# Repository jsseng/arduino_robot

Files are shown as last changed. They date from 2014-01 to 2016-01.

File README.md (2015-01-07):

arduino_robot
=============

A controllable arduino robot aimed towards elementary students to get them introduced
to computing at an early age. Comes with firmware and software including a
custom programming language tailored for simple use by students. The grammar
is defined [here](PurelyGrammar.pdf).

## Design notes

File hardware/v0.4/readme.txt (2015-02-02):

Note:  Excellon drill file resolution at 5 digits

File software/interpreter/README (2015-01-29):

To run the java program...

java Interpreter -dumpAST <STUDENT_SOURCE_FILE>

There is a script to interpret a file then avr-gcc it onto the board
It will overwrite arduino_robot/firmware/testing/main.c

./avrcompile <STUDENT_SOURCE_FILE>

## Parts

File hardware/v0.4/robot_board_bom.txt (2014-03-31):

"Qty";"Value";"Device";"Package";"Parts";"Description";"PROD_ID";"VALUE";
"1";"";"M03PTH";"1X03";"IR";"Header 3";"";"";
"3";"";"M03X22X3_SILK_SM";"2X3";"JP8, JP10, JP11";"2x3 .1" header.";"";"";
"3";"";"M04PTH";"1X04";"JP3, JP6, JP7";"Header 4";"";"";
"1";"";"M06SIP";"1X06";"JP5";"Header 6";"";"";
"2";"";"M081X08";"1X08";"JP1, JP4";"Header 8";"";"";
"2";"";"TAC_SWITCHPTH";"TACTILE-PTH";"RESET, S2";"Momentary Switch";"";"";
"5";".1uF";"C-USC1206";"C1206";"C4, C5, C6, C8, C10";"CAPACITOR, American symbol";"";"";
"1";"1.5K";"R-US_R1206";"R1206";"R53";"RESISTOR, American symbol";"";"";
"1";"100K";"R-US_R1206";"R1206";"R44";"RESISTOR, American symbol";"";"";
"2";"100K 1%";"R-US_R1206";"R1206";"R45, R46";"RESISTOR, American symbol";"";"";
"1";"100uF";"CAP_POLD";"PANASONIC_D";"C3";"Capacitor Polarized";"";"";
"8";"10K 1%";"R-US_R1206";"R1206";"R27, R37, R38, R40, R42, R54, R58, R60";"RESISTOR, American symbol";"";"";
"2";"1206PPTC_FUSE";"1206PPTC_FUSE";"R1206";"F2, F3";"";"";"";
"1";"120K 1%";"R-US_R1206";"R1206";"R35";"RESISTOR, American symbol";"";"";
"1";"16MHz";"CRYSTAL10.5X4.8";"CRYSTAL-SMD-10.5X4.8-2PIN";"Y1";"Various standard crystals. Proven footprints. Spark Fun Electronics SKU : COM-00534";"";"";
"8";"1K";"R-US_R1206";"R1206";"R39, R43, R55, R56, R59, R61, R63, R65";"RESISTOR, American symbol";"";"";
"1";"1M";"R-US_R1206";"R1206";"R28";"RESISTOR, American symbol";"";"";
"1";"1uF";"C-USC1206";"C1206";"C9";"CAPACITOR, American symbol";"";"";
"1";"1uH";"TAIYO4012";"TAIYO4012";"U$4";"";"";"";
"5";"20K 1%";"R-US_R1206";"R1206";"R23, R25, R26, R30, R32";"RESISTOR, American symbol";"";"";
"2";"22pF";"CAP0805";"0805";"C1, C2";"Capacitor";"";"";
"4";"22uF";"C-USC1206";"C1206";"C7, C11, C12, C13";"CAPACITOR, American symbol";"";"";
"2";"24K 1%";"R-US_R1206";"R1206";"R24, R31";"RESISTOR, American symbol";"";"";
"1";"2920L200";"2920L200";"SMD050F";"F1";"PolySwitch (TM) Resettable Device";"";"";
"1";"2K";"R-US_R1206";"R1206";"R62";"RESISTOR, American symbol";"";"";
"2";"2POS_TERMINAL";"2POS_TERMINAL";"2POS_TERMINAL";"U$19, U$20";"";"";"";
"1";"2X7HEADER";"2X7HEADER";"2X7";"U$1";"";"";"";
"28";"300";"R-US_R1206";"R1206";"R1, R2, R3, R4, R5, R6, R7, R8, R9, R10, R11, R12, R13, R14, R15, R16, R17, R18, R19, R20, R21, R22, R33, R34, R47, R48, R49, R50";"RESISTOR, American symbol";"";"";
"5";"330";"R-US_R1206";"R1206";"R29, R41, R51, R52, R57";"RESISTOR, American symbol";"";"";
"27";"5.1V";"DIODESOT23";"SOT23-3";"D1, D2, D3, D4, D5, D6, D7, D8, D9, D10, D11, D12, D13, D14, D15, D16, D17, D18, D19, D20, D21, D22, D26, D27, D28, D29, D32";"Diode";"";"";
"1";"600K 1%";"R-US_R1206";"R1206";"R36";"RESISTOR, American symbol";"";"";
"1";"AP431SAG-7";"AP431SAG-7";"SOT23";"U$5";"";"";"";
"1";"ATMEGA325PA";"ATMEGA325PA";"TQFP64";"U17";"";"";"";
"1";"BAT54C";"BAT54C";"SOT23";"D24";"Schottky Diodes";"";"";
"3";"BSS138";"BSS138";"SOT23";"U$9, U$10, U$11";"";"";"";
"2";"DMP2035U";"DMP2035U";"SOT23";"Q1, Q2";"Diodes Inc. DMP2035U-7 P-channel logic level mosfet";"";"";
"2";"DMP2035U-7";"DMP2035U-7";"SOT23@1";"Q3, Q4";"Diodes Inc. DMP2035U-7 P-channel logic level mosfet";"";"";
"2";"DRV8839";"DRV8839";"PWSON-N12";"U9, U10";"";"";"";
"1";"FT232RL-BASICSSOP";"FT232RL-BASICSSOP";"SSOP28DB";"U1";"USB UART";"";"";
"1";"GREEN";"LED-GREENLILYPAD";"LED-1206";"D30";"Various green LEDs";"DIO-09910";"GREEN";
"1";"HC_05";"HC_05";"BLUETOOTH_SMD";"U4";"";"";"";
"2";"LM393";"LM393";"SO08";"U12, U16";"Low-voltage comparator";"";"";
"1";"M02PTH";"M02PTH";"1X02";"JP12";"Standard 2-pin 0.1" header. Use with";"";"";
"1";"M10"";"M10"";"1X10";"JP2";"Header 10";"";"";
"1";"MIC2009A";"MIC2009A";"SOT23-M5";"U8";"";"";"";
"1";"MMA8453Q";"MMA8453Q";"QFN-COL";"U$8";"";"";"";
"4";"MOUNT-HOLE2.8";"MOUNT-HOLE2.8";"2,8";"H1, H2, H3, H4";"MOUNTING HOLE with drill center marker";"";"";
"1";"POT";"POT";"POT";"U$2";"";"";"";
"1";"POWER";"LED-GREENLILYPAD";"LED-1206";"D25";"Various green LEDs";"DIO-09910";"GREEN";
"1";"POWER_JACKPTH";"POWER_JACKPTH";"POWER_JACK_PTH";"J1";"Power Jack";"PRT-00119";"";
"2";"RX";"LED-GREENLILYPAD";"LED-1206";"D23, D34";"Various green LEDs";"DIO-09910";"GREEN";
"2";"SIA907EDJT";"SIA907EDJT";"SC70T";"U$6, U$7";"";"";"";
"1";"SW";"SW";"SW";"POWER";"";"";"";
"1";"TLV70233";"TLV70233";"SOT-23-5";"U7";"TLV70233 - 3.3V 350mA regulator";"";"";
"1";"TPS63061";"TPS63061";"WSON-10";"U$3";"TPS63031 - Step up/down 5V regulator";"";"";
"1";"USB-B";"USBPTH";"USB-B-PTH";"JP9";"USB Connectors";"CONN-08278";"USB-B";
"1";"YELLOW";"LED-GREENLILYPAD";"LED-1206";"D31";"Various green LEDs";"DIO-09910";"GREEN";

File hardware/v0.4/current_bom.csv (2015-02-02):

Qty | Value | Device | Package | Parts | Description | PROD_ID | VALUE
1 |  | M03PTH | 1X03 | IR | Header 3
3 |  | M03X22X3_SILK_SM | 2X3 | JP8, JP10, JP11 | 2x3 .1 header."
3 |  | M04PTH | 1X04 | JP3, JP6, JP7 | Header 4
1 |  | M06SIP | 1X06 | JP5 | Header 6
2 |  | M081X08 | 1X08 | JP1, JP4 | Header 8
2 |  | TAC_SWITCHPTH | TACTILE-PTH | RESET, S2 | Momentary Switch
5 | .1uF | C-USC1206 | C1206 | C4, C5, C6, C8, C10 | CAPACITOR, American symbol
1 | 1.5K 1% | R-US_R1206 | R1206 | R53 | RESISTOR, American symbol
2 | 100K 1% | R-US_R1206 | R1206 | R44, R46 | RESISTOR, American symbol
1 | 100uF | CAP_POLD | PANASONIC_D | C3 | Capacitor Polarized
7 | 10K 1% | R-US_R1206 | R1206 | R27, R37, R38, R40, R42, R58, R60 | RESISTOR, American symbol
3 | 1206PPTC_FUSE | 1206PPTC_FUSE | R1206 | F1, F2, F3
4 | 120K 1% | R-US_R1206 | R1206 | R35, R45, R64, R66 | RESISTOR, American symbol
1 | 16MHz | CRYSTAL10.5X4.8 | CRYSTAL-SMD-10.5X4.8-2PIN | Y1 | Various standard crystals. Proven footprints. Spark Fun Electronics SKU : COM-00534
9 | 1K 1% | R-US_R1206 | R1206 | R23, R39, R43, R54, R55, R56, R59, R61, R65 | RESISTOR, American symbol
1 | 1M | R-US_R1206 | R1206 | R28 | RESISTOR, American symbol
2 | 1uF | C-USC1206 | C1206 | C9, C14 | CAPACITOR, American symbol
1 | 1uH | TAIYO4012 | TAIYO4012 | U$4
4 | 20K 1% | R-US_R1206 | R1206 | R25, R26, R30, R32 | RESISTOR, American symbol
2 | 22pF | CAP0805 | 0805 | C1, C2 | Capacitor
4 | 22uF | C-USC1206 | C1206 | C7, C11, C12, C13 | CAPACITOR, American symbol
2 | 24K 1% | R-US_R1206 | R1206 | R24, R31 | RESISTOR, American symbol
1 | 2K | R-US_R1206 | R1206 | R62 | RESISTOR, American symbol
2 | 2POS_TERMINAL | 2POS_TERMINAL | 2POS_TERMINAL | U$19, U$20
1 | 2X7HEADER | 2X7HEADER | 2X7 | U$1
29 | 300 | R-US_R1206 | R1206 | R1, R2, R3, R4, R5, R6, R7, R8, R9, R10, R11, R12, R13, R14, R15, R16, R17, R18, R19, R20, R21, R22, R33, R34, R47, R48, R49, R50, R63 | RESISTOR, American symbol
5 | 330 | R-US_R1206 | R1206 | R29, R41, R51, R52, R57 | RESISTOR, American symbol
27 | 5.1V | DIODESOT23 | SOT23-3 | D1, D2, D3, D4, D5, D6, D7, D8, D9, D10, D11, D12, D13, D14, D15, D16, D17, D18, D19, D20, D21, D22, D26, D27, D28, D29, D32 | Diode
1 | 604K 1% | R-US_R1206 | R1206 | R36 | RESISTOR, American symbol
1 | AP431SAG-7 | AP431SAG-7 | SOT23 | U$5
1 | ATMEGA325PA | ATMEGA325PA | TQFP64 | U17
1 | BAT54C | BAT54C | SOT23 | D24 | Schottky Diodes
3 | BSS138 | BSS138 | SOT23 | U$9, U$10, U$11
4 | DMP2035U | DMP2035U | SOT23 | Q1, Q2, Q3, Q4 | Diodes Inc. DMP2035U-7 P-channel logic level mosfet
2 | DRV8839 | DRV8839 | PWSON-N12 | U9, U10
1 | FT232RL-BASICSSOP | FT232RL-BASICSSOP | SSOP28DB | U1 | USB UART
1 | GREEN | LED-GREENLILYPAD | LED-1206 | D30 | Various green LEDs | DIO-09910 | GREEN
1 | HC_05 | HC_05 | BLUETOOTH_SMD | U4
2 | LM393 | LM393 | SO08 | U12, U16 | Low-voltage comparator
1 | M02PTH | M02PTH | 1X02 | JP12 | Standard 2-pin 0.1 header. Use with"
1 | M10";M10"" | 1X10 | JP2 | Header 10
1 | MIC2009A | MIC2009A | SOT23-M5 | U8
1 | MMA8453Q | MMA8453Q | QFN-COL | U$8
4 | MOUNT-HOLE2.8 | MOUNT-HOLE2.8 | 2,8 | H1, H2, H3, H4 | MOUNTING HOLE with drill center marker
1 | POT | POT | POT | U$2
1 | POWER_JACKPTH | POWER_JACKPTH | POWER_JACK_PTH | J1 | Power Jack | PRT-00119
1 | PTS181224V150 | PTS181224V150 | C1812 | U$12
1 | RED | LED-GREENLILYPAD | LED-1206 | D25 | Various green LEDs | DIO-09910 | GREEN
2 | SIA907EDJT | SIA907EDJT | SC70T | U$6, U$7
1 | SW | SW | SW | POWER
1 | TLV70233 | TLV70233 | SOT-23-5 | U7 | TLV70233 - 3.3V 350mA regulator
1 | TPS63061 | TPS63061 | WSON-10 | U$3 | TPS63031 - Step up/down 5V regulator
1 | USB-B | USBPTH | USB-B-PTH | JP9 | USB Connectors | CONN-08278 | USB-B
3 | YELLOW | LED-GREENLILYPAD | LED-1206 | D23, D31, D34 | Various green LEDs | DIO-09910 | GREEN

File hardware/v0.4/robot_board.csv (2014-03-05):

Qty | Value | Device | Package | Parts | Description | PROD_ID | VALUE
1 |  | M03PTH | 1X03 | IR | Header 3
3 |  | M03X22X3_SILK_SM | 2X3 | JP8, JP10, JP11 | 2x3 .1 header."
3 |  | M04PTH | 1X04 | JP3, JP6, JP7 | Header 4
2 |  | M06SIP | 1X06 | JP4, JP5 | Header 6
1 |  | M081X08 | 1X08 | JP1 | Header 8
2 |  | TAC_SWITCHPTH | TACTILE-PTH | RESET, S2 | Momentary Switch
4 | .1uF | C-USC1206 | C1206 | C4, C5, C6, C8 | CAPACITOR, American symbol
1 | 1.5K | R-US_R1206 | R1206 | R53 | RESISTOR, American symbol
1 | 10 | R-US_R1206 | R1206 | R64 | RESISTOR, American symbol
1 | 100K | R-US_R1206 | R1206 | R44 | RESISTOR, American symbol
1 | 100uF | CAP_POLD | PANASONIC_D | C3 | Capacitor Polarized
7 | 10K 1% | R-US_R1206 | R1206 | R27, R28, R40, R42, R45, R46, R54 | RESISTOR, American symbol
1 | 1206PPTC_FUSE | 1206PPTC_FUSE | R1206 | F2
1 | 15K 1% | R-US_R1206 | R1206 | R29 | RESISTOR, American symbol
1 | 16MHz | CRYSTAL10.5X4.8 | CRYSTAL-SMD-10.5X4.8-2PIN | Y1 | Various standard crystals. Proven footprints. Spark Fun Electronics SKU : COM-00534
7 | 1K | R-US_R1206 | R1206 | R39, R43, R55, R56, R59, R61, R63 | RESISTOR, American symbol
1 | 1uF | C-USC1206 | C1206 | C9 | CAPACITOR, American symbol
1 | 2.4V | DIODESOT23 | SOT23-3 | D23 | Diode
9 | 20K 1% | R-US_R1206 | R1206 | R23, R25, R26, R30, R31, R32, R33, R34, R36 | RESISTOR, American symbol
2 | 22pF | CAP0805 | 0805 | C1, C2 | Capacitor
1 | 22uF | C-USC1206 | C1206 | C7 | CAPACITOR, American symbol
1 | 27K 1% | R-US_R1206 | R1206 | R24 | RESISTOR, American symbol
1 | 2920L200 | 2920L200 | SMD050F | F1 | PolySwitch (TM) Resettable Device
1 | 2K | R-US_R1206 | R1206 | R62 | RESISTOR, American symbol
2 | 2POS_TERMINAL | 2POS_TERMINAL | 2POS_TERMINAL | U$19, U$20
26 | 300 | R-US_R1206 | R1206 | R1, R2, R3, R4, R5, R6, R7, R8, R9, R10, R11, R12, R13, R14, R15, R16, R17, R18, R19, R20, R21, R22, R47, R48, R49, R50 | RESISTOR, American symbol
2 | 300K 1% | R-US_R1206 | R1206 | R58, R60 | RESISTOR, American symbol
4 | 330 | R-US_R1206 | R1206 | R41, R51, R52, R57 | RESISTOR, American symbol
2 | 4.7K | R-US_R1206 | R1206 | R37, R38 | RESISTOR, American symbol
27 | 5.1V | DIODESOT23 | SOT23-3 | D1, D2, D3, D4, D5, D6, D7, D8, D9, D10, D11, D12, D13, D14, D15, D16, D17, D18, D19, D20, D21, D22, D26, D27, D28, D29, D32 | Diode
1 | 5K 1% | R-US_R1206 | R1206 | R35 | RESISTOR, American symbol
1 | ATMEGA325PA | ATMEGA325PA | TQFP64 | U17
1 | BAT54C | BAT54C | SOT23 | D33 | Schottky Diodes
2 | DMP2035U | DMP2035U | SOT23 | Q1, Q2 | Diodes Inc. DMP2035U-7 P-channel logic level mosfet
2 | DMP2035U-7 | DMP2035U-7 | SOT23@1 | Q3, Q4 | Diodes Inc. DMP2035U-7 P-channel logic level mosfet
2 | DRV8839 | DRV8839 | PWSON-N12 | U9, U10
1 | FT232RL-BASICSSOP | FT232RL-BASICSSOP | SSOP28DB | U1 | USB UART
1 | GREEN | LED-GREENLILYPAD | LED-1206 | D30 | Various green LEDs | DIO-09910 | GREEN
1 | HC_05 | HC_05 | BLUETOOTH_SMD | U4
3 | LM393 | LM393 | SO08 | U11, U12, U16 | Low-voltage comparator
1 | M08X2 | M08X2 | 2X8 | U$1 | .1 headers, two rows of 8 each"
1 | M10";M10"" | 1X10 | JP2 | Header 10
1 | MIC2009A | MIC2009A | SOT23-M5 | U8
1 | MIC5219 | MIC52055V | SOT23-5 | U3 | MIC5205 150mA vreg | VREG-00823
1 | MMA8453Q | MMA8453Q | QFN-COL | U$8
4 | MOUNT-HOLE2.8 | MOUNT-HOLE2.8 | 2,8 | H1, H2, H3, H4 | MOUNTING HOLE with drill center marker
1 | POT | POT | POT | U$2
1 | POWER | LED-GREENLILYPAD | LED-1206 | D25 | Various green LEDs | DIO-09910 | GREEN
1 | POWER_JACKPTH | POWER_JACKPTH | POWER_JACK_PTH | J1 | Power Jack | PRT-00119
1 | RX | LED-GREENLILYPAD | LED-1206 | D34 | Various green LEDs | DIO-09910 | GREEN
3 | SIA907EDJT | SIA907EDJT | SC70T | U2, U5, U6
1 | SW | SW | SW | POWER
1 | TLV70233 | TLV70233 | SOT-23-5 | U7 | TLV70233 - 3.3V 350mA regulator
1 | USB-B | USBPTH | USB-B-PTH | JP9 | USB Connectors | CONN-08278 | USB-B
1 | YELLOW | LED-GREENLILYPAD | LED-1206 | D31 | Various green LEDs | DIO-09910 | GREEN

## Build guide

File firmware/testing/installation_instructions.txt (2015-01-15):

Mac installation instructions 

1.  install Mac Crosspack:  http://www.obdev.at/products/crosspack/index.html

  This will install gcc for the AVR microcontroller and other related tools.

2.  plug in the board and turn the board on

3.  edit the Makefile

  Find the 'usbprogram' target in the Makefile in this directory and change the device to the usb device on your computer.  It should look something like this:  /dev/tty.usbserial-A602FK45.  Look for the device in the /dev directory and it should show up as something with tty.usbserial.

4.  type 'make' to compile the code in this directory

5.  type 'make usbprogram' to flash the microcontroller.

  The board should start running your code once the flashing is complete.

--------------------------------------------------------------------------

Linux installation instructions

1.  install the avr toolchain on Ubuntu using:  

   apt-get install avrdude binutils-avr avr-libc gcc-avr

2.  plug in the board and turn the board on

3.  follow steps 3-5 from the Mac instructions

   NOTE:  The device on Ubuntu may look like /dev/ttyUSB0.

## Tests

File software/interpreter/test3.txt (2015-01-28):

define thermometer = analogPinIn[0]
define leftServo = servo[0]
define rightServo = servo[1]

when start
{
   display "Hello! Machine is starting up"
}

repeat
{
   display "Thermometer reading is: " + get thermometer
   set leftServo 15
   set rightServo 75

   display "Temperature in Celsius is: " + ((get thermometer - 32) * 5 / 9)
}

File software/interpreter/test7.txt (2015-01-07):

# This is a big test

define tL = motor[0]
define tR = motor[1]
define bL = motor[2]
define bR = motor[3]

define s1 = servo[0]
define s2 = servo[1]
define s3 = servo[2]

define thermometer = analogPinIn[0]
define ir = analogPinIn[1]

define gX = gyroscope[X]
define gY = gyroscope[Y]
define gZ = gyroscope[Z]

variable i = 0
variable f = 0.0

variable iArr[10] = 5
variable fArr[99] = 4.4

func turnLeft()
{
   set tL 30
   set tR 60
   set bL 30
   set bR 60
   return 0
}

func turnRight()
{
   set tL 60
   set tR 30
   set bL 60
   set bR 30
   return 0
}

func halt()
{
   set tL 0
   set tR 0
   set bL 0
   set bR 0
   return 0
}

func go()
{
   set tL 70
   set tR 70
   set bL 70
   set bR 70
   return 0
}

when get thermometer > 15
{
   halt()
}

when get ir eq 4
{
   set s1 50
   set s2 100
}

when get gX > 100 and get gY > 100
{
   display "Both X and Y > 100"
}

when thermometer changes 
{
}

when get button equals 1
{
   stop
}
fArr[1000] = 5.5

turnLeft()
sleep 4

repeat 4 times
{
   sleep iArr[5] * 6
}

iArr[2] = 5
fArr[1000] = 5.5

go()

repeat 
{
}

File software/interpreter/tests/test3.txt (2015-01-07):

define front_right = motor[1]
define front_left = motor[2]
define back_left = motor[3]
define back_right = motor[4]

when start {
     display "Hello! May the force be with you \n and may the odds be ever in your favor!"
     startMoving()
}

func startMoving() {
     repeat 4 {
         move forward x > 4
	 move forward 3
	 turn left
	 move forward 5
	 turn left 
	 move forward 3
	 turn left
	 move forward 5
	 turn right
	 move backward 4
	 turn left 
	 move backward 5
     }     

     display "I'm dizzy!"
}

when get back_right > 0 {
     stop
}

stop

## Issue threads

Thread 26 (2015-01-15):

Board does not reset on powerup

jsseng, 2015-01-15:
The board does not automatically reset on powerup.

Closed 2015-01-18.

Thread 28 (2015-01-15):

change power switch

jsseng, 2015-01-15:
Change the power switch to one that is horizontal to prevent interference with shields.

jsseng, 2015-01-16:
Replace with part:  0S102011MA1QN1

Closed 2015-01-21.

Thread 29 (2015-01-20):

add some hysteresis to USB voltage comparator

jsseng, 2015-01-20:

jsseng, 2015-01-21:
fixed

Closed 2015-01-21.

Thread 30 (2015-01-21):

board does not power when USB and 5V battery applied

jsseng, 2015-01-21:
To reproduce:

1.  Connect both USB cable and ~5V battery power
2.  Turn on the board
3.  Remove the USB cable

The board will power off even though power is applied through the battery and the power switch is on.  At that point, if the board is power cycled everything will work fine again.

jsseng, 2015-01-21:
fixed

Closed 2015-01-21.

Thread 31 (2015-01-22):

board draws excessive USB power when battery is 2.8V

jsseng, 2015-01-22:
To reproduce:

1.  Apply 2.8V to the battery input
2.  Connect the USB cable to a computer

The LCD on the board will flicker indicating unstable power (sometimes this will cause the computer to reboot).  This does not occur with all computers.

jsseng, 2015-02-02:
fixed in latest revision

Closed 2015-02-02.

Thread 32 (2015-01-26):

running make from the software directory has compile errors

jsseng, 2015-01-26:
1.  did a git clone
2.  ran make from arduino_robot/software/interpreter

java version 1.7.0_71

ooee123, 2015-01-28:
Fixed compilation errors. Some .java files didn't make it in the commit and push, and patched missing methods.

Closed 2015-01-28.

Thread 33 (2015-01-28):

avg-gcc atmega325pa not recognized

ooee123, 2015-01-28:
On my version of Ubuntu installed on a Chromebook, my avr-gcc complains of an unrecognized mmcu of atmega325pa. For the meanwhile, the board seems to accept the mmcu substitute of atmega325.

Running the Makefile located in arduino_robot/firmware/testing/Makefile:
fd
Here's the error message
```
#avr-gcc -DF_CPU=20000000L -Wall -mmcu=atmega325pa -O2 -o main.elf main.c adc.c servo.c motor.c lcd.c utility.c i2c.c
avr-gcc -I../library -DF_CPU=20000000L -Wall -mmcu=atmega325pa -O2 -o main.elf main.c ../library/adc.c ../library/i2c.c ../library/lcd.c ../library/motor.c ../library/servo.c ../library/utility.c
avr-gcc: error: unrecognized argument in option ‘-mmcu=atmega325pa’
avr-gcc: note: valid arguments to ‘-mmcu=’ are: at43usb320 at43usb355 at76c711 at86rf401 at90c8534 at90can128 at90can32 at90can64 at90pwm1 at90pwm161 at90pwm2 at90pwm216 at90pwm2b at90pwm3 at90pwm316 at90pwm3b at90pwm81 at90s1200 at90s2313 at90s2323 at90s2333 at90s2343 at90s4414 at90s4433 at90s4434 at90s8515 at90s8535 at90scr100 at90usb1286 at90usb1287 at90usb162 at90usb646 at90usb647 at90usb82 at94k ata5272 ata5505 ata5790 ata5790n ata5795 ata6285 ata6286 ata6289 atmega103 atmega128 atmega1280 atmega1281 atmega1284 atmega1284p atmega128a atmega128rfa1 atmega16 atmega161 atmega162 atmega163 atmega164a atmega164p atmega164pa atmega165 atmega165a atmega165p atmega165pa atmega168 atmega168a atmega168p atmega168pa atmega169 atmega169a atmega169p atmega169pa atmega16a atmega16hva atmega16hva2 atmega16hvb atmega16hvbrevb atmega16m1 atmega16u2 atmega16u4 atmega2560 atmega2561 atmega26hvg atmega32 atmega323 atmega324a atmega324p atmega324pa atmega325 atmega3250 atmega3250a atmega3250p atmega3250pa atmega325a atmega325p atmega328 atmega328p atmega329 atmega3290 atmega3290a atmega3290p atmega3290pa atmega329a atmega329p atmega329pa atmega32a atmega32c1 atmega32hvb atmega32hvbrevb atmega32m1 atmega32u2 atmega32u4 atmega32u6 atmega406 atmega48 atmega48a atmega48hvf atmega48p atmega48pa atmega64 atmega640 atmega644 atmega644a atmega644p atmega644pa atmega645 atmega6450 atmega6450a atmega6450p atmega645a atmega645p atmega649 atmega6490 atmega6490a atmega6490p atmega649a atmega649p atmega64a atmega64c1 atmega64hve atmega64m1 atmega64rfa2 atmega64rfr2 atmega8 atmega8515 atmega8535 atmega88 atmega88a atmega88p atmega88pa atmega8a atmega8hva atmega8u2 atmxt112sl atmxt224 atmxt224e atmxt336s atmxt540s atmxt540sreva attiny11 attiny12 attiny13 attiny13a attiny15 attiny1634 attiny167 attiny22 attiny2313 attiny2313a attiny24 attiny24a attiny25 attiny26 attiny261 attiny261a attiny28 attiny4313 attiny43u attiny44 attiny44a attiny45 attiny461 attiny461a attiny48 attiny84 attiny84a attiny85 attiny861 attiny861a attiny87 attiny88 atxmega128a1 atxmega128a1u atxmega128a3 atxmega128a3u atxmega128a4u atxmega128b1 atxmega128b3 atxmega128c3 atxmega128d3 atxmega128d4 atxmega16a4 atxmega16a4u atxmega16c4 atxmega16d4 atxmega16x1 atxmega192a3 atxmega192a3u atxmega192c3 atxmega192d3 atxmega256a3 atxmega256a3b atxmega256a3bu atxmega256a3u atxmega256c3 atxmega256d3 atxmega32a4 atxmega32a4u atxmega32c4 atxmega32d4 atxmega32e5 atxmega32x1 atxmega384c3 atxmega384d3 atxmega64a1 atxmega64a1u atxmega64a3 atxmega64a3u atxmega64a4u atxmega64b1 atxmega64b3 atxmega64c3 atxmega64d3 atxmega64d4 avr1 avr2 avr25 avr3 avr31 avr35 avr4 avr5 avr51 avr6 avrxmega2 avrxmega4 avrxmega5 avrxmega6 avrxmega7 m3000
make: *** [main] Error 1
```

And finally my avr-gcc version
```
Using built-in specs.
COLLECT_GCC=avr-gcc
COLLECT_LTO_WRAPPER=/usr/lib/gcc/avr/4.8.2/lto-wrapper
Target: avr
Configured with: ../src/configure -v --enable-languages=c,c++ --prefix=/usr/lib --infodir=/usr/share/info --mandir=/usr/share/man --bindir=/usr/bin --libexecdir=/usr/lib --libdir=/usr/lib --enable-shared --with-system-zlib --enable-long-long --enable-nls --without-included-gettext --disable-libssp --build=x86_64-linux-gnu --host=x86_64-linux-gnu --target=avr
Thread model: single
gcc version 4.8.2 (GCC)
```

jsseng, 2015-01-28:
I am running gcc 4.8.1 and it supports the ATMega325pa.  What distribution of Ubuntu are you running?  I will try to install a VM to check the versions.

Closed 2015-02-03.

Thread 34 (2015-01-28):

add command line option to output different C versions

jsseng, 2015-01-28:
Add a command line option to generate C code that can compile either on the Arduino or the host machine.  Currently it generates code that will only run on the host machine.

jsseng, 2015-02-06:
I don't think we need this anymore.

Closed 2015-02-06.

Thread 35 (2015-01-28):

problem compiling _arrayCheck

jsseng, 2015-01-28:
I ran this through the parser:

    when start {
       display "hello"
       }

I got this which gave me compile errors with the _arrayCheck function:

```
#include <stdio.h>
#include <stdlib.h>

int _arrayCheck(int size, int index) { if (index >= size) { fprintf(stderr, "Index out of bounds
"); exit(0); } return index; }
int chng_temp;
void start(void)
{
printf("%s\n","hello");
}
void repeatAlways(void)
{
}
int main(void) {
start();
while (1) {
repeatAlways();
}
return 0;
}
```

jsseng, 2015-01-28:
Nevermind, it was a line break problem when saving the file.

Closed 2015-01-28.

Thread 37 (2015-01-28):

missing semicolons in output

jsseng, 2015-01-28:
Try this:

```
define i = analogPinIn[0]

when start {
   variable a = 0
   variable b = 0
   display "hello"
   a = get i
   b = get i
   }

```

ooee123, 2015-01-29:
Thanks, got it to work again. Semi colons added and new lines added for assignment statements.

Update in a couple of hours on taking generated C-code and compiling it for atmega

Closed 2015-01-29.

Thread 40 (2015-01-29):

Name the board and programming language

jsseng, 2015-01-29:
Post your top 2 animals.  Be sure to check for any related projects with similar names.

aaronkeen, 2015-01-29:
Rhinoceros
Wallaby

ooee123, 2015-01-29:
Aardvark
Flamingo

aaronkeen, 2015-01-29:
I almost said Flamingo.  Mostly because of the idea of frying the board and the obvious link 'Flaming-o'.

jsseng, 2015-02-05:
Toucan
Puffin

Although I just found a couple of bird-named kids robot projects:  Finch and Hummingbird.  There was also a Puffin web browser.

lanahodzic, 2015-02-05:
Bumble bee and that language could be Buzz

Or

Cow and the language could be Moo
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

Closed 2015-02-05.

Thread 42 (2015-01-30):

when statements and when not

ooee123, 2015-01-30:
I made a fairly neat discovery that our language supports without planning for it.
```
when get button {
  ...code...
}

when not get button {
   ... otherwise do this...
}
```

You can insert a not between the when and the expression. It's useful for assigning a "default behavior" to do when a button is not toggled. like set the LED to be off.

Language wise, it would be a good idea to combine them by joining them by an "else"
Will explore.

Closed 2015-02-11.

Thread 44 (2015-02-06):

java.lang.Exception: Stack trace

jsseng, 2015-02-06:
first line of buzz input file is:

```
define test = serv[3]
```

The error is
```
java.lang.Exception: Stack trace
	at java.lang.Thread.dumpStack(Thread.java:1364)
	at parser.Parser.error(Parser.java:1324)
	at parser.Parser.expected(Parser.java:1319)
	at parser.Parser.parseMachinery(Parser.java:249)
	at parser.Parser.parseDeclarations(Parser.java:185)
	at parser.Parser.parseProgram(Parser.java:27)
	at parser.Parser.parse(Parser.java:20)
	at Interpreter.main(Interpreter.java:16)
```

ooee123, 2015-02-06:
I think it should work for servo[3]

Typo?
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

jsseng, 2015-02-06:
I was intentionally testing with the typo.

Closed 2015-02-11.

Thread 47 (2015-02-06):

remove 'left' and 'right' keywords

jsseng, 2015-02-06:
I tried this and I get an error:

```
define right = motor[1]
```

ooee123, 2015-02-11:
That was an old artifact from early design iterations. Will remove.

Closed 2015-02-11.

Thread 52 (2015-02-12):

swap RX and TX labels on the board

jsseng, 2015-02-12:

Closed 2015-02-17.

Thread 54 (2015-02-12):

test CY7C65213-28PVXI

jsseng, 2015-02-12:
The CY7C65213-28PVXI is a USB-UART and is pin compatible with the current FT232R.  The FT232R Mac driver is causing the reboots.

jsseng, 2015-02-18:
The new chip works on Linux and home Mac.  Before closing the ticket, add 1uF capacitor and disconnect DNU pin.

jsseng, 2015-02-18:
Fixed.  No more Mac reboots.

Closed 2015-02-18.

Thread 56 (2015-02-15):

add servo power protection

jsseng, 2015-02-15:
I found a wire shorting combination that will instantly damage the board.  The odds of running into this error are small, but I will add a small protection circuit that can be easily disabled if it causes some problems.  This way, we do not have to do another board revision.

The other option is to just not fix the problem.

Closed 2015-02-23.

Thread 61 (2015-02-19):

'repeat' always requires 'times' keyword

jsseng, 2015-02-19:
I tried this, but it did not like it and required the 'times' keyword after the expression:

```
repeat (x<6) {
	x = x+1
}
```

ooee123, 2015-02-25:
Hmm, we can make a strong case for the word "while"

The current intent of repeat is for a loop to occur X times. Now, I can also imagine a case like this
```
repeat while (x < 6) {
   x = x + 1
}
```
That can be done. As a matter of syntax, for a while loop, would we prefer a repeat keyword or a while without a repeat keyword like this:
```
while x < 6 {
   x = x + 1
}
```

ooee123, 2015-02-25:
Oh, and
```
repeat (x < 6) times {
   x = x + 1
}
```
would let x < 6 evaluate in C style (resulting in the number 0 or 1), so that loop would happen exactly 0 or 1 times.
We can detect if the expression is a conditional expression, then one of two things can happen:
1) Warn the user that "Perhaps you mean to use a repeat while?"
2) From the detection of the conditional expression, convert that repeat into a while on our translated C.

I'm going to take the warn the user route for now, we can discuss.

ooee123, 2015-02-28:
OKAY, as per our discussion last Thursday 2/26:
```
repeat _expression_ {
}
```
Will evaluate as a while. Notice the missing keyword "times"
In addition, I included a warning if the conditional expression is not really a boolean. For example
```
repeat x {
   x = 4 < y
}
```
Will create a warning.

Closed 2015-02-28.

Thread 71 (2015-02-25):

SetCursor parameters

ooee123, 2015-02-25:
The set cursor parameters no longer require parenthesis, so the following is approved:

```
set cursor 0 5
```
Where the first parameter is the row [0, 1] and the second parameter is the column [0, 7]

Right now, the limits start counting at 0.
In addition, there is no error checking if the parameters are outside the bounds of appropriate cursor placement

ooee123, 2015-04-21:
It prints an error to the LCD screen if the row or col are out of bounds on runtime

Closed 2015-04-21.

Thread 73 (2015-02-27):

loop runs 1 time

jsseng, 2015-02-27:
I'm not sure if this issue is related to the other loop issue, but here is the code I used:

```
var x = 1
repeat x < 10 times {
	clear
	display x
	sleep 1000
	x = x + 1
}
```

This generates the following C which runs once:

```
{
int rptCnt;
for (rptCnt = 0; rptCnt < (x < 10); rptCnt++)
{
clear_screen();
sprintf(_printBuffer, "%d",x);
print_string(_printBuffer);
_delay_ms(1000);
x = (x + 1);
}
}
```

Closed 2015-03-01.

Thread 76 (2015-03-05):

Rename gyroscopes -> accel

ooee123, 2015-03-05:
Since accel's are always on the board, they should be constants in the language, similar to
led1, led2, and button.

ooee123, 2015-04-21:
Done

Closed 2015-04-21.

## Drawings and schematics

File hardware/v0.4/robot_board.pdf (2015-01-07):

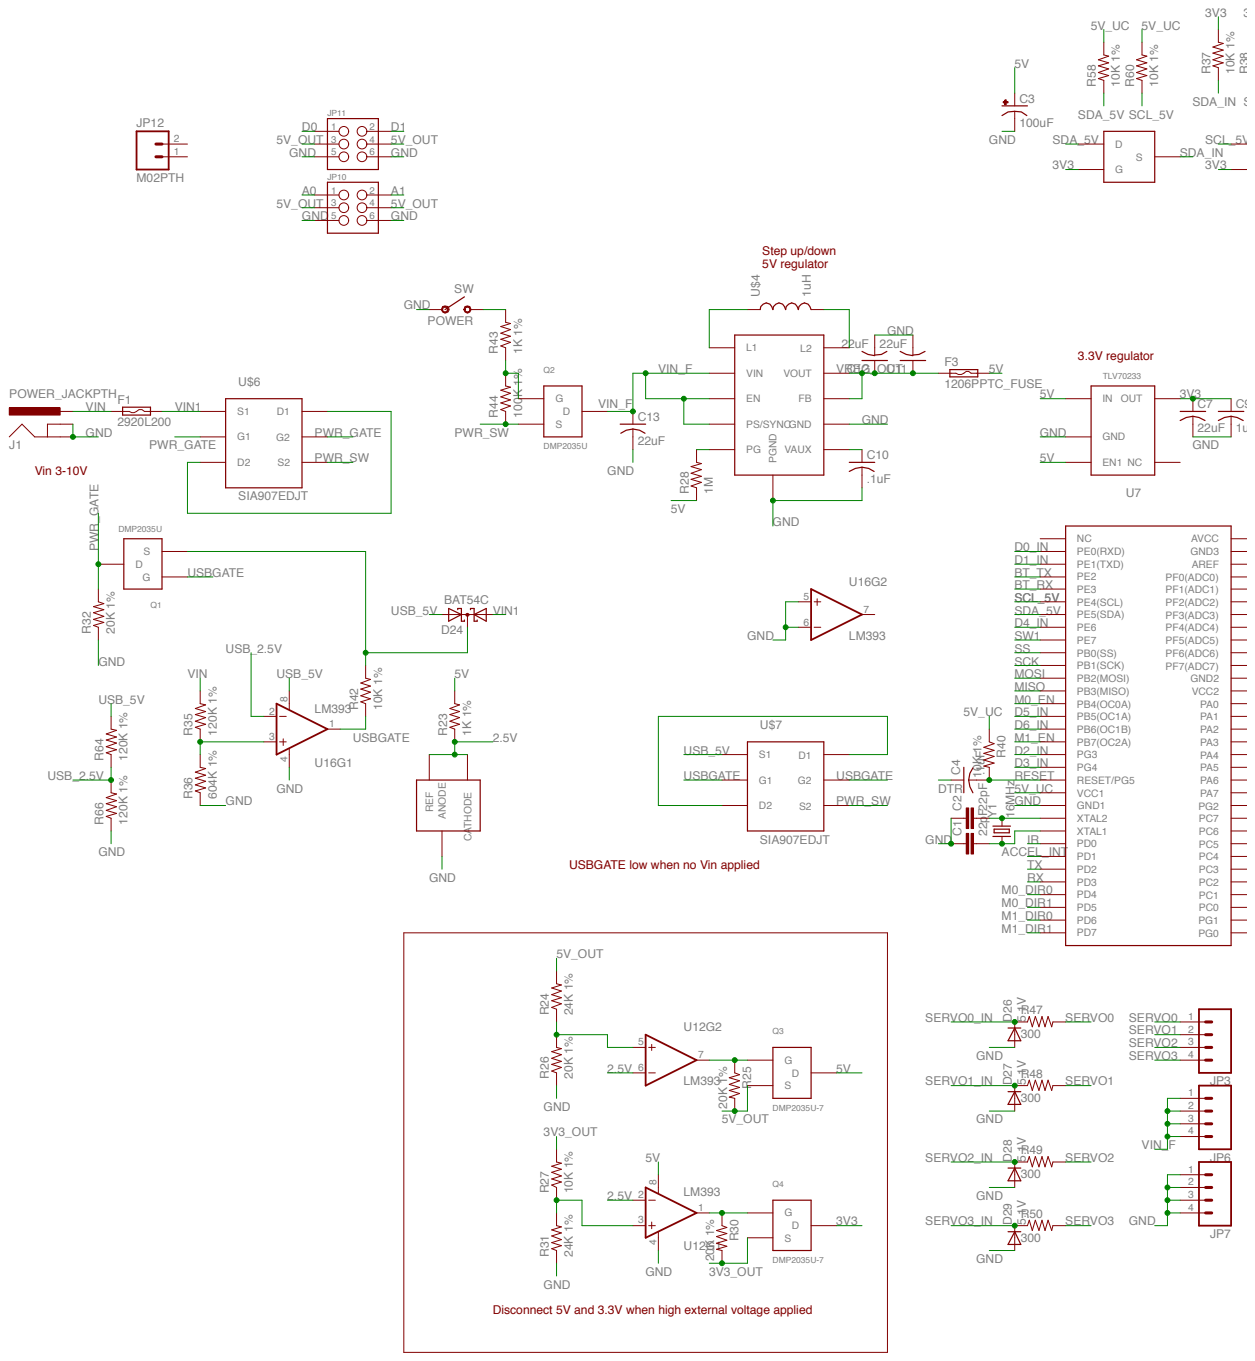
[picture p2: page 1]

USBGATE low when no Vin applied

Disconnect 5V and 3.3V when high external voltage applied

# VCC GND_PPAD GND

# VCC GND_PPAD GND

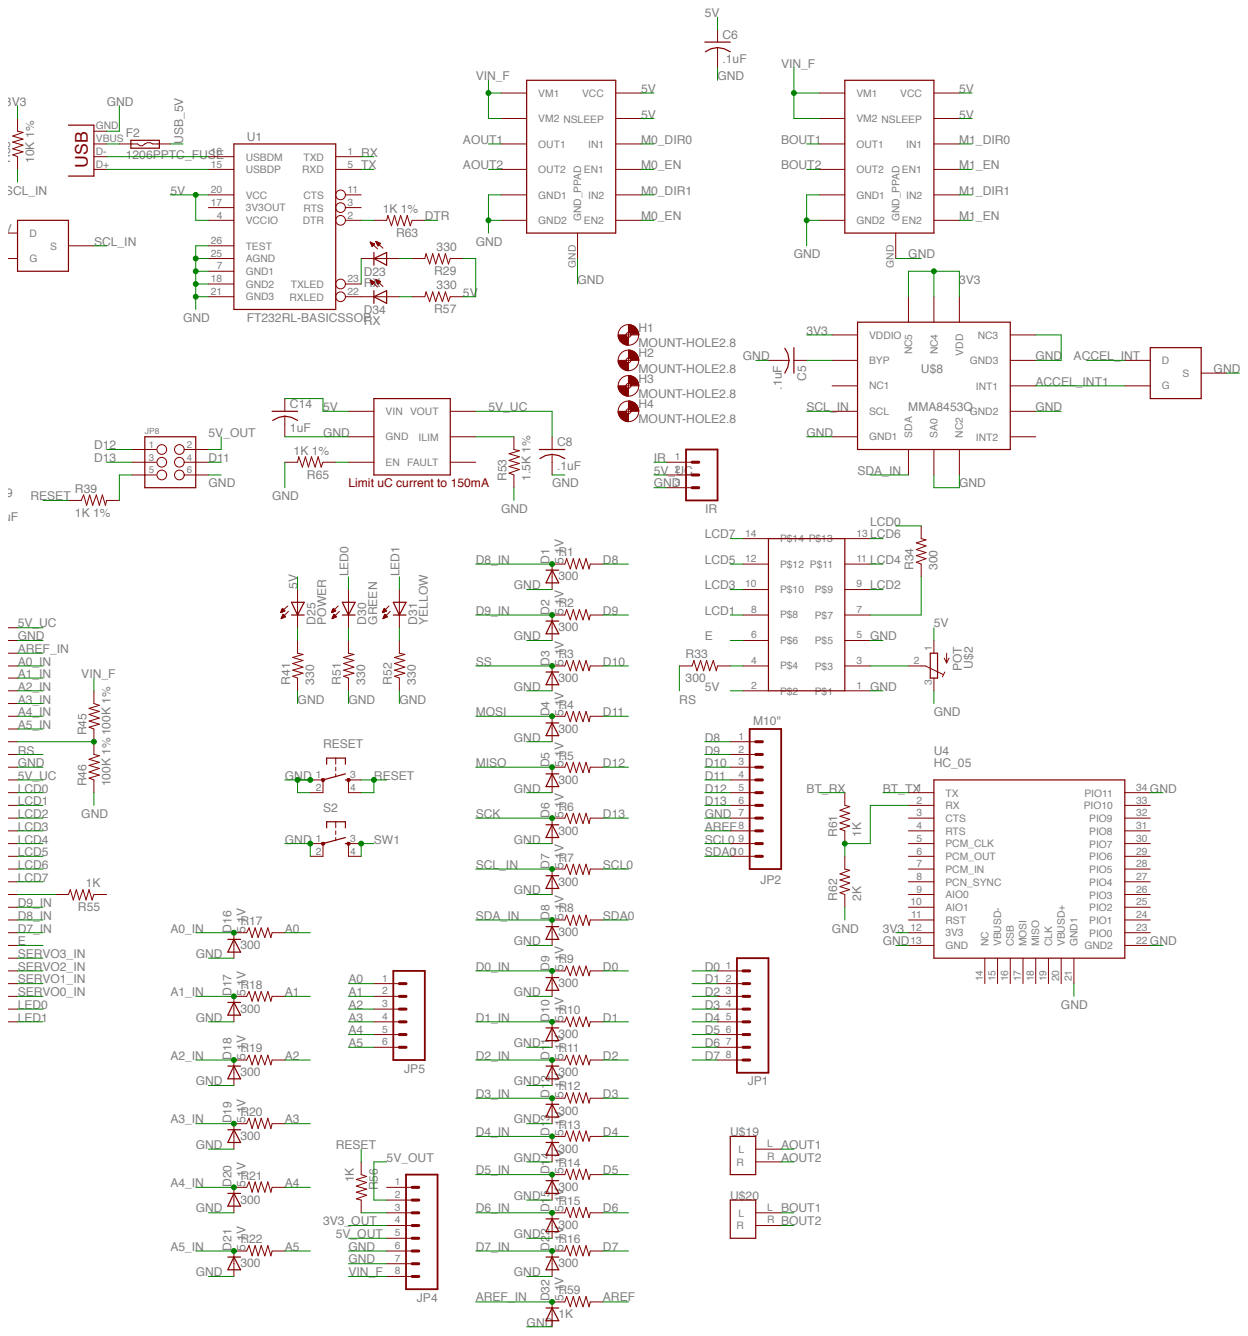
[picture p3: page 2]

EN FAULT
Limit uC current to 150mA

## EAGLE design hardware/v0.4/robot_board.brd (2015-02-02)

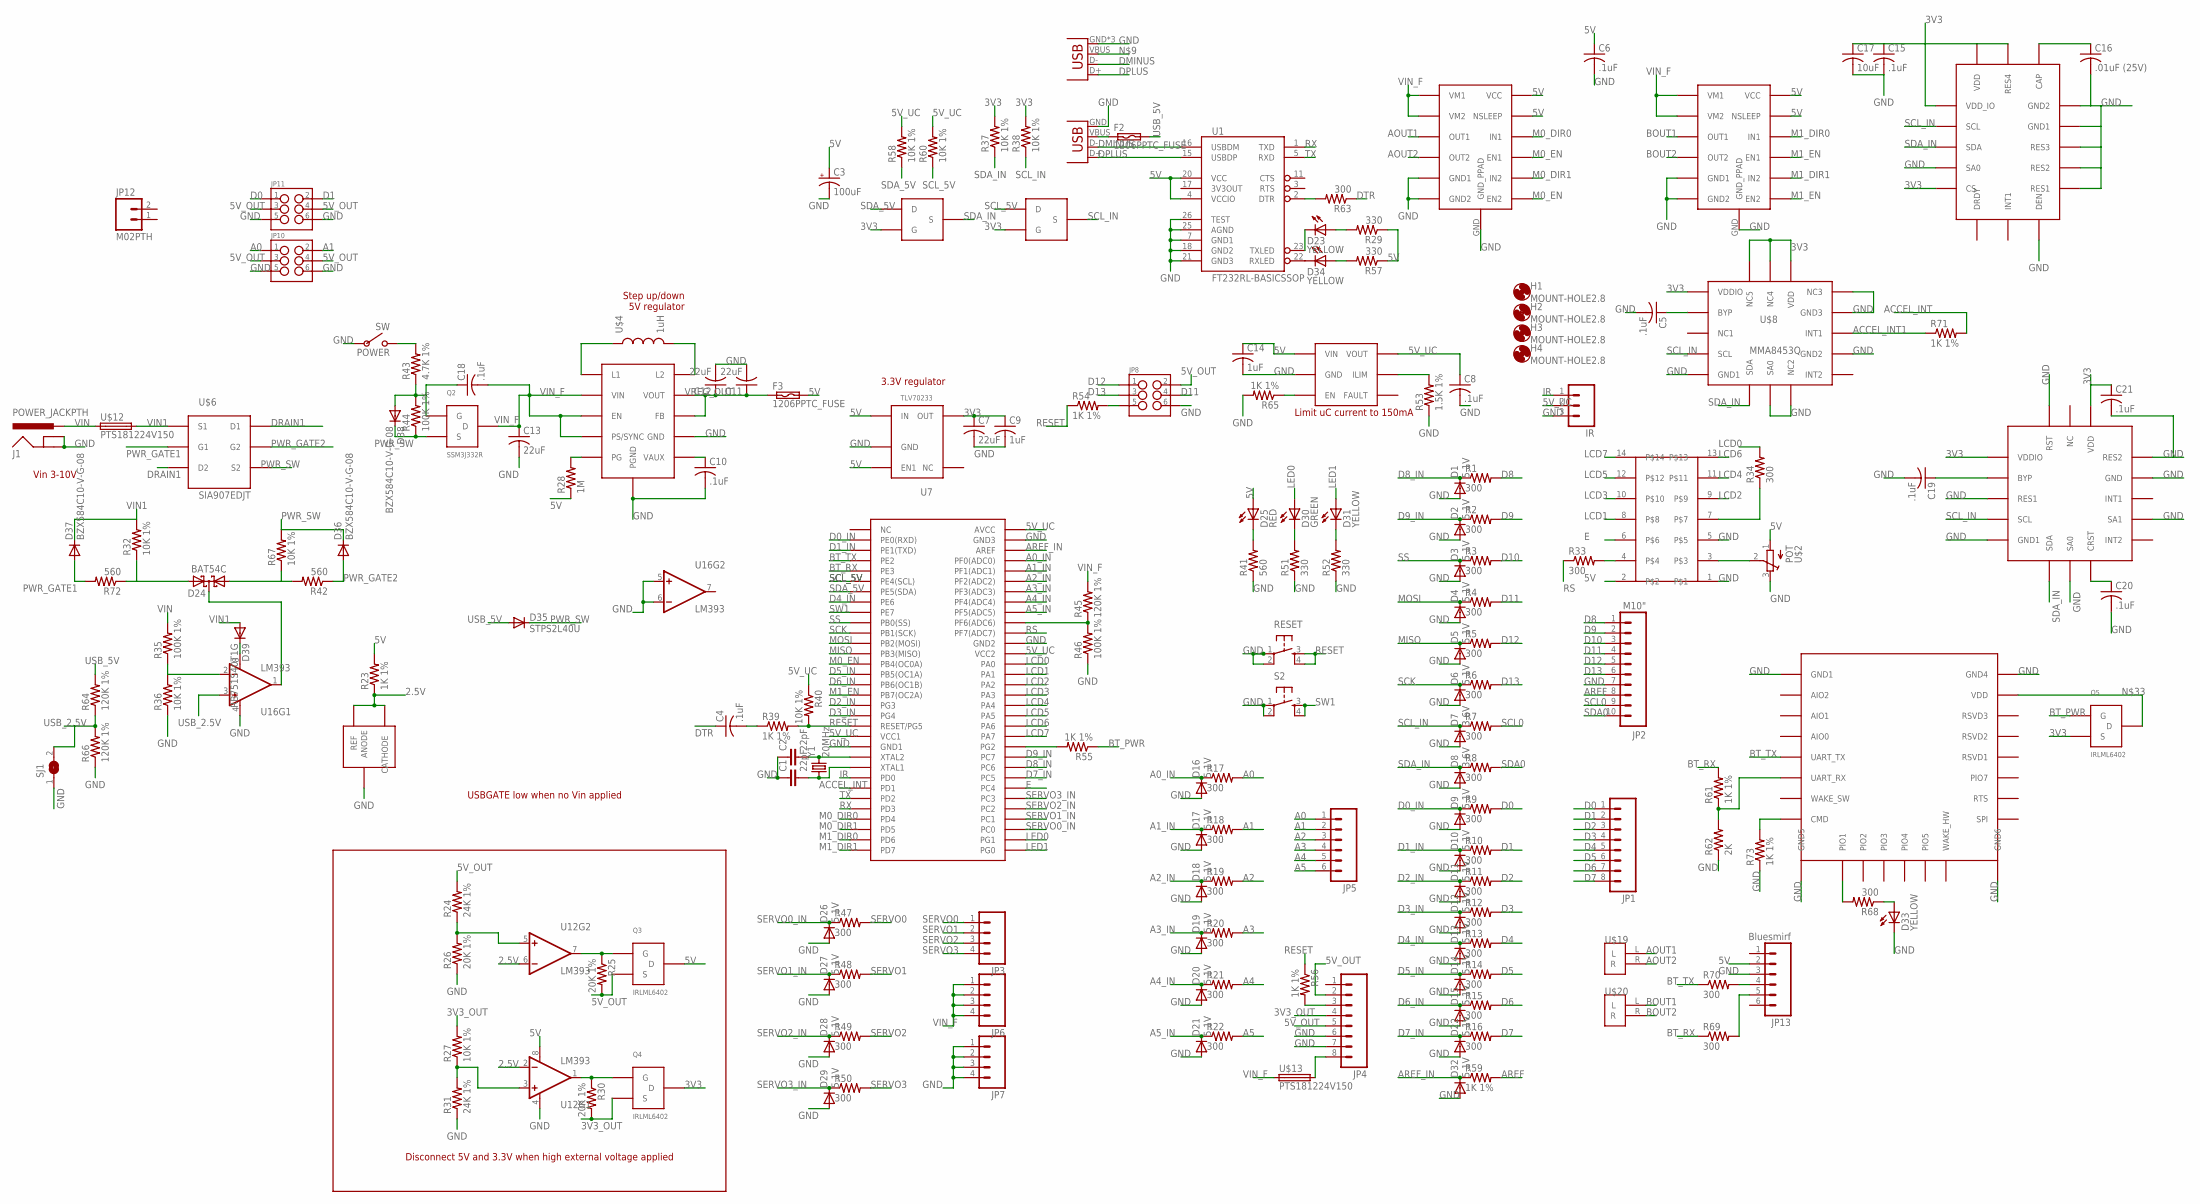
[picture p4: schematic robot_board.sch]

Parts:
C1, C2: 22pF; 0805
C3: 100uF; PANASONIC_D
C4, C5, C6, C8, C10, C15, C18, C19, C20, C21: .1uF; C1206
C7, C11, C12, C13: 22uF; C1206
C9, C14: 1uF; C1206
C16: .01uF (25V); C1206
C17: 10uF; C1206
D1, D2, D3, D4, D5, D6, D9, D10, D11, D12, D13, D14, D15, D16, D17, D18, D19, D20, D21, D22, D26, D27, D28, D29, D32: 5.1V; SOT23-3
D7, D8: 3.6V; SOT23-3
D23, D31, D33, D34: YELLOW; LED-1206
D24: BAT54C; SOT23
D25: RED; LED-1206
D30: GREEN; LED-1206
D35: STPS2L40U; SMA-DIODE
D36, D37, D38: BZX584C10-V-G-08; SOD523
D39: RB751S40T1G; SOD523
F2, F3: 1206PPTC_FUSE; R1206
H1, H2, H3, H4: MOUNT-HOLE2.8; 2,8
IR: M03PTH; 1X03
J1: POWER_JACKPTH; POWER_JACK_PTH
JP1, JP4: M081X08; 1X08
JP2: M10"; 1X10
JP3, JP6, JP7: M04PTH; 1X04
JP5: M06SIP; 1X06
JP8, JP10, JP11: M03X22X3_SILK_SM; 2X3
JP9: USB-B; USB-B-PTH
JP12: M02PTH; 1X02
JP13: Bluesmirf; 1X06
JP14: USB-MICROB
POWER: SW
Q2: SSM3J332R; SOT23
Q3, Q4, Q5: IRLML6402; SOT23
R1, R2, R3, R4, R5, R6, R7, R8, R9, R10, R11, R12, R13, R14, R15, R16, R17, R18, R19, R20, R21, R22, R33, R34, R47, R48, R49, R50, R63, R68, R69, R70: 300; R1206
R23, R39, R54, R55, R56, R59, R61, R65, R71, R73: 1K 1%; R1206
R24, R31: 24K 1%; R1206
R25, R26, R30: 20K 1%; R1206
R27, R32, R36, R37, R38, R40, R58, R60, R67: 10K 1%; R1206
R28: 1M; R1206
R29, R51, R52, R57: 330; R1206
R35, R44, R46: 100K 1%; R1206
R41, R42, R72: 560; R1206
R43: 4.7K 1%; R1206
R45, R64, R66: 120K 1%; R1206
R53: 1.5K 1%; R1206
R62: 2K; R1206
RESET: TAC_SWITCHPTH; TACTILE-PTH
S2: TAC_SWITCHPTH; TACTILE-PTH
SJ1: SJW
U1: FT232RL-BASICSSOP; SSOP28DB
U7: TLV70233; SOT-23-5
U8: MIC2009A; SOT23-M5
U9, U10: DRV8839; PWSON-N12
U12, U16: LM393; SO08
U17: ATMEGA325PA; TQFP64
U$1: 2X7HEADER; 2X7
U$2: POT
U$3: TPS63061; WSON-10
U$4: 1uH; TAIYO4012
U$5: AP431SAG-7; SOT23
U$6: SIA907EDJT; SC70T
U$7: RN4020; RN4020_PKG
U$8: MMA8453Q; QFN-COL
U$9, U$10: BSS138; SOT23
U$11: L3GD20HTR; LGA-16
U$12, U$13: PTS181224V150; C1812
U$14: FXOS8700CQ; FSOS8700CQ_PKG
U$19, U$20: 2POS_TERMINAL
Y1: 20MHz; CRYSTAL-SMD-10.5X4.8-2PIN

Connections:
2.5V: R23.1, U12.2 (-IN), U12.6 (-IN), U$5.1 (CATHODE), U$5.2 (REF)
3V3: C7.1, C9.1, C15.1, C17.1, C21.1, Q4.3 (D), Q5.2 (S), R37.2, R38.2, U7.P$4 (OUT), U$8.P$1 (VDDIO), U$8.P$14 (VDD), U$8.P$15 (NC4), U$8.P$16 (NC5), U$9.1 (G), U$10.1 (G), U$11.P$1 (VDD_IO), U$11.P$5 (CS), U$11.P$15 (RES4), U$11.P$16 (VDD), U$14.P$1 (VDDIO), U$14.P$14 (VDD)
3V3_OUT: JP4.4, Q4.2 (S), R27.2, R30.2
5V: C3.+, C6.1, C14.1, D25.A, F3.2, JP13.2, Q3.3 (D), R23.2, R28.1, R29.1, R57.1, U1.4 (VCCIO), U1.20 (VCC), U7.P$1 (IN), U7.P$3 (EN1), U8.P$1 (VIN), U9.P$7 (VCC), U9.P$8 (NSLEEP), U10.P$7 (VCC), U10.P$8 (NSLEEP), U12.8 (V+), U$1.2, U$2.1 (A)
5V_OUT: JP4.2, JP4.5, JP8.2, JP10.3, JP10.4, JP11.3, JP11.4, Q3.2 (S), R24.2, R25.2
5V_UC: C8.1, IR.2, R40.1, R58.2, R60.2, U8.P$6 (VOUT), U17.21 (VCC1), U17.52 (VCC2), U17.64 (AVCC)
A0: JP5.1, JP10.1, R17.2
A0_IN: D16.3 (C), R17.1, U17.61 (PF0(ADC0))
A1: JP5.2, JP10.2, R18.2
A1_IN: D17.3 (C), R18.1, U17.60 (PF1(ADC1))
A2: JP5.3, R19.2
A2_IN: D18.3 (C), R19.1, U17.59 (PF2(ADC2))
A3: JP5.4, R20.2
A3_IN: D19.3 (C), R20.1, U17.58 (PF3(ADC3))
A4: JP5.5, R21.2
A4_IN: D20.3 (C), R21.1, U17.57 (PF4(ADC4))
A5: JP5.6, R22.2
A5_IN: D21.3 (C), R22.1, U17.56 (PF5(ADC5))
ACCEL_INT: R71.2, U17.26 (PD1)
ACCEL_INT1: R71.1, U$8.P$11 (INT1)
AOUT1: U9.P$3 (OUT1), U$19.L
AOUT2: U9.P$4 (OUT2), U$19.R
AREF: JP2.8, R59.2
AREF_IN: D32.3 (C), R59.1, U17.62 (AREF)
BOUT1: U10.P$3 (OUT1), U$20.L
BOUT2: U10.P$4 (OUT2), U$20.R
BT_PWR: Q5.1 (G), R55.1
BT_RX: R61.2, R69.1, U17.5 (PE3)
BT_TX: R70.1, U17.4 (PE2), U$7.P$5 (UART_TX)
D0: JP1.1, JP11.1, R9.2
D0_IN: D9.3 (C), R9.1, U17.2 (PE0(RXD))
D1: JP1.2, JP11.2, R10.2
D1_IN: D10.3 (C), R10.1, U17.3 (PE1(TXD))
D2: JP1.3, R11.2
D2_IN: D11.3 (C), R11.1, U17.18 (PG3)
D3: JP1.4, R12.2
D3_IN: D12.3 (C), R12.1, U17.19 (PG4)
D4: JP1.5, R13.2
D4_IN: D13.3 (C), R13.1, U17.8 (PE6)
D5: JP1.6, R14.2
D5_IN: D14.3 (C), R14.1, U17.15 (PB5(OC1A))
D6: JP1.7, R15.2
D6_IN: D15.3 (C), R15.1, U17.16 (PB6(OC1B))
D7: JP1.8, R16.2
D7_IN: D22.3 (C), R16.1, U17.40 (PC5)
D8: JP2.1, R1.2
D8_IN: D1.3 (C), R1.1, U17.41 (PC6)
D9: JP2.2, R2.2
D9_IN: D2.3 (C), R2.1, U17.42 (PC7)
D10: JP2.3, R3.2
D11: JP2.4, JP8.4, R4.2
D12: JP2.5, JP8.1, R5.2
D13: JP2.6, JP8.3, R6.2
DMINUS: JP9.D-, JP14.D-, U1.16 (USBDM)
DPLUS: JP9.D+, JP14.D+, U1.15 (USBDP)
DRAIN1: U$6.D1@1 (D1), U$6.D1@2 (D1), U$6.D2@1 (D2), U$6.D2@2 (D2)
DTR: C4.1, R63.1
E: U17.39 (PC4), U$1.6
GND: C1.1, C2.1, C3.-, C5.2, C6.2, C7.2, C8.2, C9.2, C10.2, C11.2, C12.2, C13.2, C14.2, C15.2, C16.2, C17.2, C19.2, C20.2, C21.2, D1.1 (A), D2.1 (A), D3.1 (A), D4.1 (A), D5.1 (A), D6.1 (A), D7.1 (A), D8.1 (A), D9.1 (A), D10.1 (A), D11.1 (A), D12.1 (A), D13.1 (A), D14.1 (A), D15.1 (A), D16.1 (A), D17.1 (A), D18.1 (A), D19.1 (A), D20.1 (A), D21.1 (A), D22.1 (A), D26.1 (A), D27.1 (A), D28.1 (A), D29.1 (A), D32.1 (A), D33.C, IR.3, J1.GND, J1.GNDBREAK, JP2.7, JP4.6, JP4.7, JP7.1, JP7.2, JP7.3, JP7.4, JP8.6, JP9.GND, JP10.5, JP10.6, JP11.5, JP11.6, JP13.3, JP14.GND, JP14.MT1 (GND), JP14.MT2 (GND), POWER.P$2, R26.1, R31.1, R36.1, R41.1, R46.1, R51.1, R52.1, R53.1, R62.1, R65.2, R66.1, R73.1, RESET.1, RESET.2, S2.1, S2.2, SJ1.1, U1.7 (GND1), U1.18 (GND2), U1.21 (GND3), U1.25 (AGND), U1.26 (TEST), U7.P$2 (GND), U8.P$2 (GND), U9.GND (GND_PPAD), U9.P$5 (GND1), U9.P$6 (GND2), U10.GND (GND_PPAD), U10.P$5 (GND1), U10.P$6 (GND2), U12.4 (V-), U16.4 (V-), U16.5 (+IN), U16.6 (-IN), U17.22 (GND1), U17.53 (GND2), U17.63 (GND3), U$1.1, U$1.5, U$2.3 (E), U$3.GND@N1 (PGND), U$3.GND@N2 (PGND), U$3.GND@N3 (PGND), U$3.GND@N4 (PGND), U$3.GND@N5 (PGND), U$3.GND@N6 (PGND), U$3.GND@N7 (PGND), U$3.GND@N8 (PGND), U$3.P$7 (GND), U$3.P$11 (PGND), U$5.3 (ANODE), U$7.P$1 (GND1), U$7.P$22 (GND4), U$7.P$23 (GND5), U$7.P$24 (GND6), U$8.P$5 (GND1), U$8.P$7 (SA0), U$8.P$8 (NC2), U$8.P$10 (GND2), U$8.P$12 (GND3), U$8.P$13 (NC3), U$11.P$4 (SA0), U$11.P$8 (DEN), U$11.P$9 (RES1), U$11.P$10 (RES2), U$11.P$11 (RES3), U$11.P$12 (GND1), U$11.P$13 (GND2), U$14.P$3 (RES1), U$14.P$5 (GND1), U$14.P$7 (SA0), U$14.P$10 (SA1), U$14.P$12 (GND), U$14.P$13 (RES2), U$14.P$16 (RST)
IR: IR.1, U17.25 (PD0)
LCD0: R34.2, U17.51 (PA0)
LCD1: U17.50 (PA1), U$1.8
LCD2: U17.49 (PA2), U$1.9
LCD3: U17.48 (PA3), U$1.10
LCD4: U17.47 (PA4), U$1.11
LCD5: U17.46 (PA5), U$1.12
LCD6: U17.45 (PA6), U$1.13
LCD7: U17.44 (PA7), U$1.14
LED0: D30.A, U17.34 (PG1)
LED1: D31.A, U17.33 (PG0)
M0_DIR0: U9.P$9 (IN1), U17.29 (PD4)
M0_DIR1: U9.P$11 (IN2), U17.30 (PD5)
M0_EN: U9.P$10 (EN1), U9.P$12 (EN2), U17.14 (PB4(OC0A))
M1_DIR0: U10.P$9 (IN1), U17.31 (PD6)
M1_DIR1: U10.P$11 (IN2), U17.32 (PD7)
M1_EN: U10.P$10 (EN1), U10.P$12 (EN2), U17.17 (PB7(OC2A))
MISO: D5.3 (C), R5.1, U17.13 (PB3(MISO))
MOSI: D4.3 (C), R4.1, U17.12 (PB2(MOSI))
unnamed: C2.2, U17.23 (XTAL2), Y1.P$2 (2)
unnamed: C1.2, U17.24 (XTAL1), Y1.P$1 (1)
unnamed: R53.2, U8.P$5 (ILIM)
unnamed: R55.2, U17.43 (PG2)
unnamed: JP4.3, R56.2
unnamed: C5.1, U$8.P$2 (BYP)
unnamed: F2.1, JP9.VBUS, JP14.VBUS
unnamed: D34.C, U1.22 (RXLED)
unnamed: D34.A, R57.2
unnamed: D23.A, R29.2
unnamed: R61.1, R62.2, U$7.P$6 (UART_RX)
unnamed: R63.2, U1.2 (DTR)
unnamed: U$1.3, U$2.2 (S)
unnamed: R28.2, U$3.P$5 (PG)
unnamed: R65.1, U8.P$3 (EN)
unnamed: D24.3 (CC), U16.1 (OUT)
unnamed: C10.1, U$3.P$6 (VAUX)
unnamed: U$3.P$1 (L1), U$4.P$1 (1)
unnamed: U$3.P$10 (L2), U$4.P$2 (2)
unnamed: D23.C, U1.23 (TXLED)
unnamed: D24.2 (A2), R32.1, R72.1
unnamed: D24.1 (A1), R42.2, R67.1
unnamed: R33.2, U$1.4
unnamed: R34.1, U$1.7
unnamed: C4.2, R39.1
unnamed: JP4.8, U$13.2
unnamed: JP8.5, R54.2
unnamed: Q3.1 (G), R25.1, U12.7 (OUT)
unnamed: R68.2, U$7.P$9 (PIO1)
unnamed: D33.A, R68.1
unnamed: Q5.3 (D), U$7.P$21 (VDD)
unnamed: R24.1, R26.2, U12.5 (+IN)
unnamed: JP13.4, R70.2
unnamed: JP13.5, R69.2
unnamed: C16.1, U$11.P$14 (CAP)
unnamed: R27.1, R31.2, U12.3 (+IN)
unnamed: R35.1, R36.2, U16.2 (-IN)
unnamed: D25.C, R41.2
unnamed: D39.C, U16.8 (V+)
unnamed: POWER.P$1, R43.2
unnamed: C19.1, U$14.P$2 (BYP)
unnamed: Q4.1 (G), R30.1, U12.1 (OUT)
unnamed: R73.2, U$7.P$8 (CMD)
unnamed: C20.1, U$14.P$8 (CRST)
unnamed: C18.1, D38.A, Q2.1 (G), R43.1, R44.2
unnamed: R45.1, R46.2, U17.55 (PF6(ADC6))
unnamed: D30.C, R51.2
unnamed: D31.C, R52.2
PWR_GATE1: D37.A, R72.2, U$6.G1
PWR_GATE2: D36.A, R42.1, U$6.G2
PWR_SW: D35.C, D36.C, D38.C, Q2.2 (S), R44.1, R67.2, U$6.S2
RESET: R39.2, R40.2, R54.1, R56.1, RESET.3, RESET.4, U17.20 (RESET/PG5)
RS: R33.1, U17.54 (PF7(ADC7))
RX: U1.1 (TXD), U17.28 (PD3)
SCK: D6.3 (C), R6.1, U17.11 (PB1(SCK))
SCL0: JP2.9, R7.2
SCL_5V: R60.1, U17.6 (PE4(SCL)), U$10.3 (D)
SCL_IN: D7.3 (C), R7.1, R38.1, U$8.P$4 (SCL), U$10.2 (S), U$11.P$2 (SCL), U$14.P$4 (SCL)
SDA0: JP2.10, R8.2
SDA_5V: R58.1, U17.7 (PE5(SDA)), U$9.3 (D)
SDA_IN: D8.3 (C), R8.1, R37.1, U$8.P$6 (SDA), U$9.2 (S), U$11.P$3 (SDA), U$14.P$6 (SDA)
SERVO0: JP3.1, R47.2
SERVO0_IN: D26.3 (C), R47.1, U17.35 (PC0)
SERVO1: JP3.2, R48.2
SERVO1_IN: D27.3 (C), R48.1, U17.36 (PC1)
SERVO2: JP3.3, R49.2
SERVO2_IN: D28.3 (C), R49.1, U17.37 (PC2)
SERVO3: JP3.4, R50.2
SERVO3_IN: D29.3 (C), R50.1, U17.38 (PC3)
SS: D3.3 (C), R3.1, U17.10 (PB0(SS))
SW1: S2.3, S2.4, U17.9 (PE7)
TX: U1.5 (RXD), U17.27 (PD2)
USB_2.5V: R64.1, R66.2, SJ1.2, U16.3 (+IN)
USB_5V: D35.A, F2.2, R64.2
VIN: J1.PWR, R35.2, U$12.1
VIN1: D37.C, D39.A, R32.2, U$6.S1, U$12.2
VIN_F: C13.1, C18.2, JP6.1, JP6.2, JP6.3, JP6.4, Q2.3 (D), R45.2, U9.P$1 (VM1), U9.P$2 (VM2), U10.P$1 (VM1), U10.P$2 (VM2), U$3.P$2 (VIN), U$3.P$3 (EN), U$3.P$4 (PS/SYNC), U$13.1
VREG_OUT: C11.1, C12.1, F3.1, U$3.P$8 (FB), U$3.P$9 (VOUT)

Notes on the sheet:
USBGATE low when no Vin applied
3.3V regulator
Disconnect 5V and 3.3V when high external voltage applied
Limit uC current to 150mA
Step up/down 5V regulator
Vin 3-10V

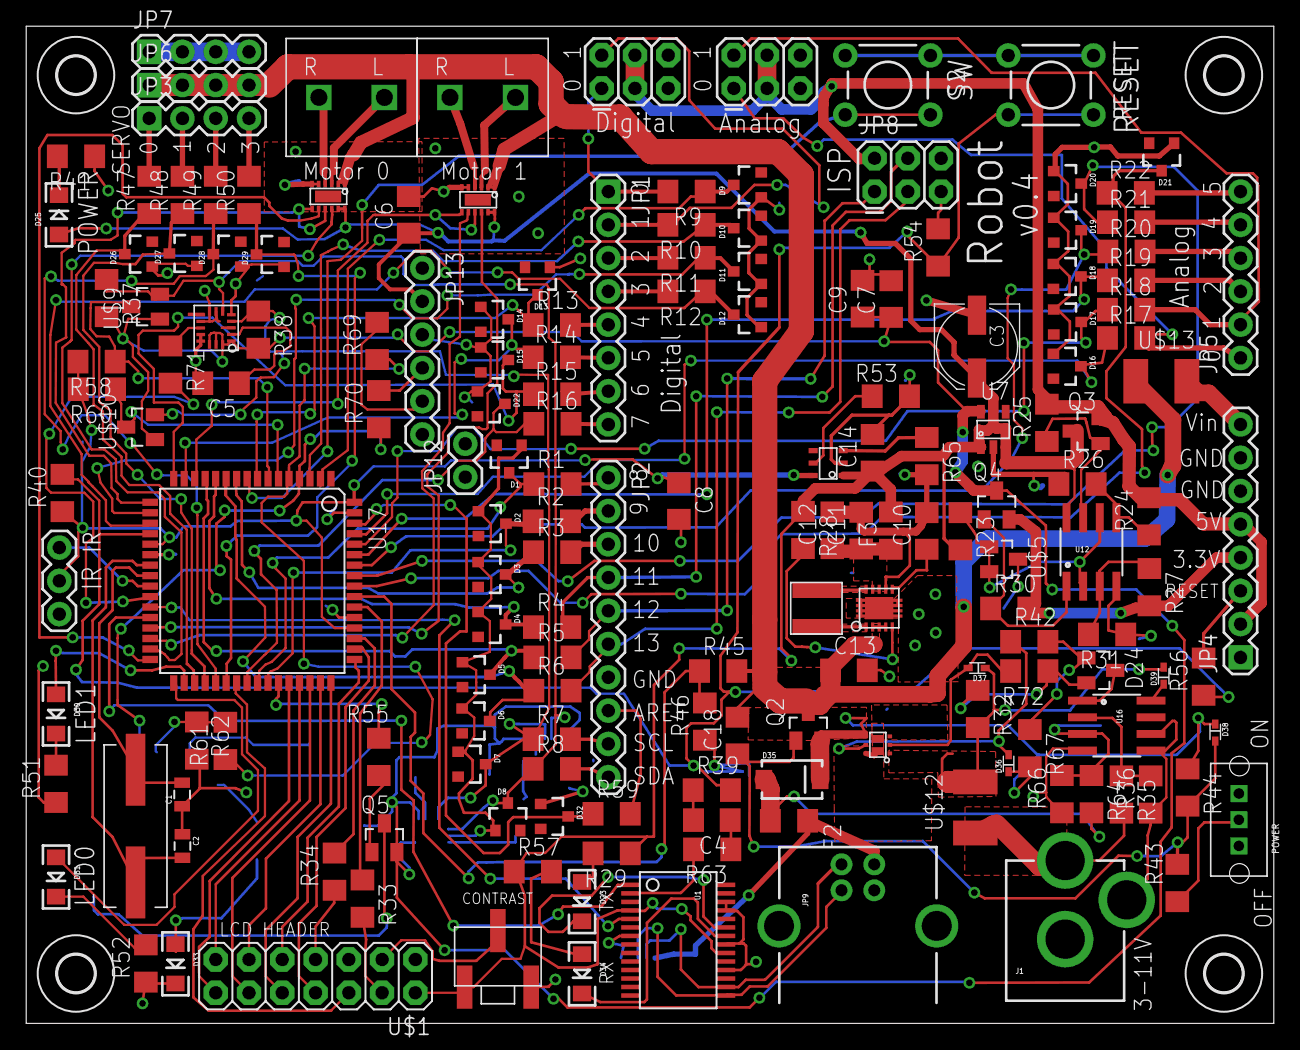
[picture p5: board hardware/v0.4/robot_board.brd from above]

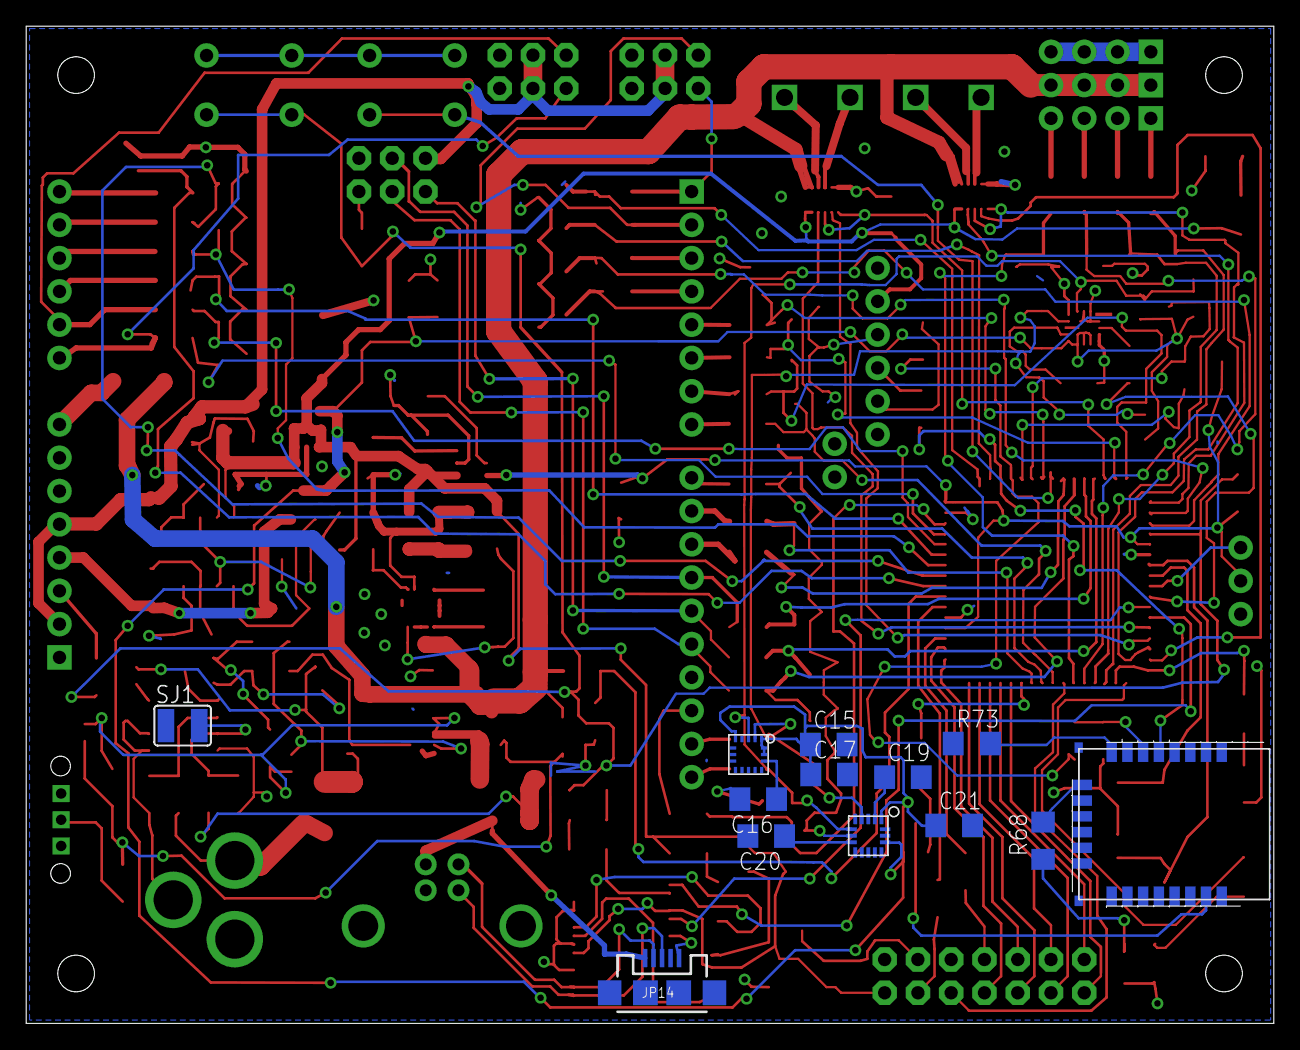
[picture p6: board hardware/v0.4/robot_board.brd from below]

Board: 2 copper layers, 95.2 x 76.1 mm, 188 parts (13 on the bottom side), 156 nets.

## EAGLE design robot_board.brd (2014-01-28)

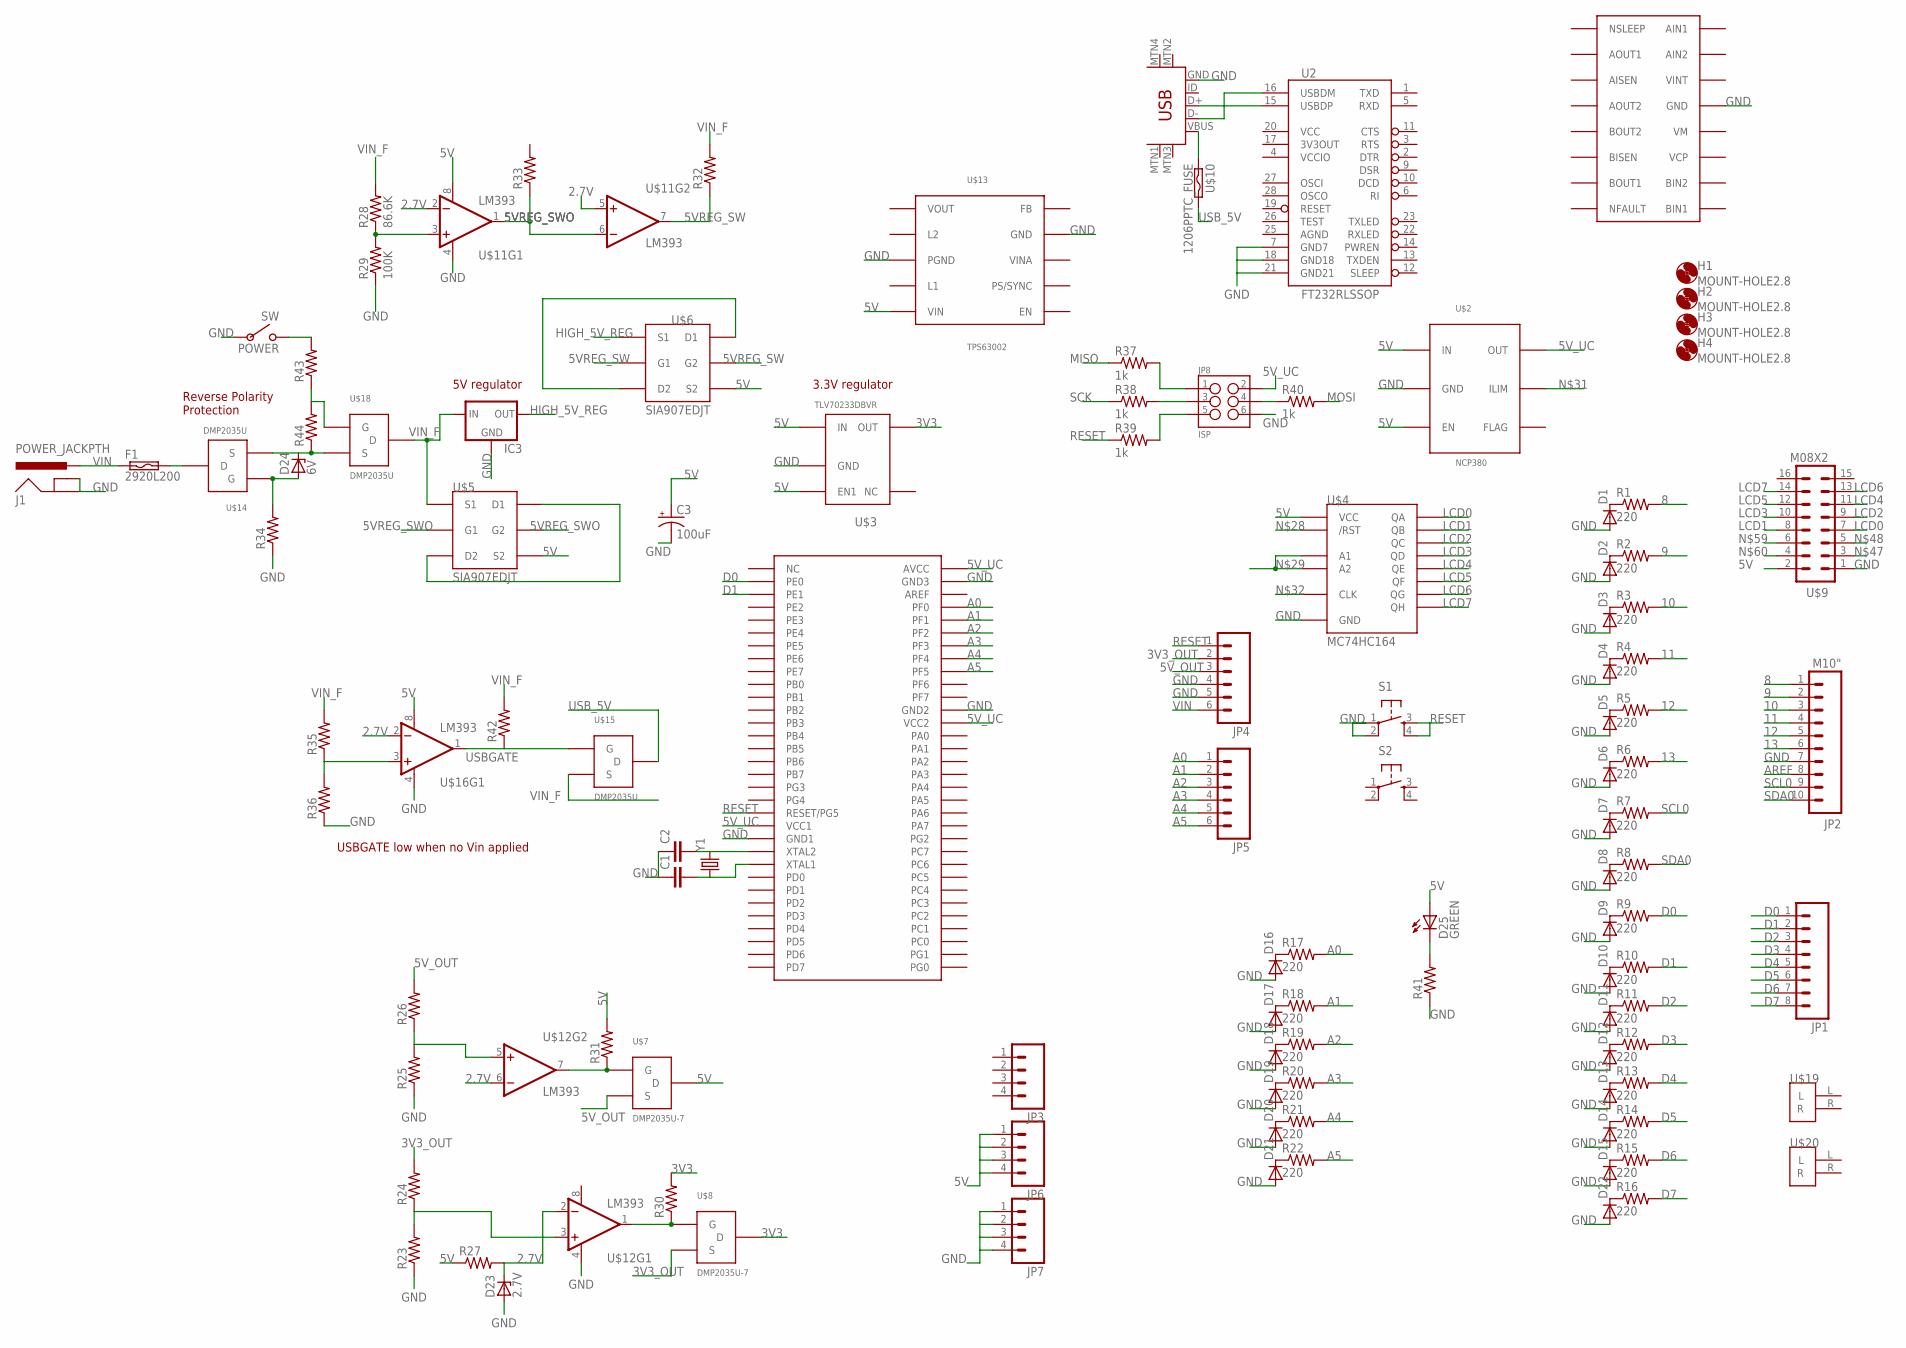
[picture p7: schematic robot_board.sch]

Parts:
C1, C2: CAP0805; 0805
C3: 100uF; PANASONIC_D
D1, D2, D3, D4, D5, D6, D7, D8, D9, D10, D11, D12, D13, D14, D15, D16, D17, D18, D19, D20, D21, D22: DIODESOT23; SOT23-3
D23: 2.7V; SOD80C
D24: 6V; SOD80C
D25: GREEN; LED-1206
F1: 2920L200; SMD050F
H1, H2, H3, H4: MOUNT-HOLE2.8; 2,8
IC3: 78XXS
J1: POWER_JACKPTH; POWER_JACK_PTH
JP1: M081X08; 1X08
JP2: M10"; 1X10
JP3, JP6, JP7: M04PTH; 1X04
JP4, JP5: M06SIP; 1X06
JP8: ISP; 2X3
POWER: SW
R1, R2, R3, R4, R5, R6, R7, R8, R9, R10, R11, R12, R13, R14, R15, R16, R17, R18, R19, R20, R21, R22: 220; R1206
R23, R24, R25, R26, R27, R30, R31, R32, R33: R-US_R0805; R0805
R28: 86.6K; R0805
R29: 100K; R0805
R34, R35, R36, R41, R42, R43, R44: R-US_R1206; R1206
R37, R38, R39, R40: 1k; R1206
S1, S2: TAC_SWITCHPTH; TACTILE-PTH
U2: FT232RLSSOP; SSOP28DB
U$1: USB-MINIB-5PIN; USB-MINIB
U$2: NCP380; TSOP-5
U$3: TLV70233DBVR; SOT-23-5
U$4: MC74HC164; TSSOP-14
U$5, U$6: SIA907EDJT; SC70T
U$7, U$8: DMP2035U-7; SOT23
U$9: M08X2; 2X8
U$10: 1206PPTC_FUSE; R1206
U$11, U$12, U$16: LM393; SO08
U$13: TPS63002; 10SON
U$14, U$15, U$18: DMP2035U; SOT23
U$17: ATMEGA325PA; TQFP64
U$19, U$20: 2POS_TERMINAL
U$21: DRV8833; TSSOP16
Y1: CRYSTAL10.5X4.8; CRYSTAL-SMD-10.5X4.8-2PIN

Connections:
2.7V: D23.C, R27.2, U$11.2 (-IN), U$11.5 (+IN), U$12.2 (-IN), U$12.6 (-IN), U$16.2 (-IN)
3V3: R30.2, U$3.P$4 (OUT), U$8.3 (D)
3V3_OUT: JP4.2, R24.2, U$8.2 (S)
5V: C3.+, D25.A, JP6.1, JP6.2, JP6.3, JP6.4, R27.1, R31.2, U$2.P$4 (IN), U$2.P$6 (EN), U$3.P$1 (IN), U$3.P$3 (EN1), U$4.14 (VCC), U$5.P$4 (S2), U$6.P$4 (S2), U$7.3 (D), U$9.2, U$11.8 (V+), U$13.P$5 (VIN), U$16.8 (V+)
5VREG_SW: R32.1, U$6.P$2 (G1), U$6.P$5 (G2), U$11.7 (OUT)
5VREG_SWO: R33.1, U$5.P$2 (G1), U$5.P$5 (G2), U$11.1 (OUT), U$11.6 (-IN)
5V_OUT: JP4.3, R26.2, U$7.2 (S)
5V_UC: JP8.2, U$2.P$1 (OUT), U$17.21 (VCC1), U$17.52 (VCC2), U$17.64 (AVCC)
8: JP2.1, R1.2
9: JP2.2, R2.2
10: JP2.3, R3.2
11: JP2.4, R4.2
12: JP2.5, R5.2
13: JP2.6, R6.2
A0: JP5.1, R17.2, U$17.61 (PF0)
A1: JP5.2, R18.2, U$17.60 (PF1)
A2: JP5.3, R19.2, U$17.59 (PF2)
A3: JP5.4, R20.2, U$17.58 (PF3)
A4: JP5.5, R21.2, U$17.57 (PF4)
A5: JP5.6, R22.2, U$17.56 (PF5)
AGND: U2.25 (AGND)
AREF: JP2.8
D0: JP1.1, R9.2, U$17.2 (PE0)
D1: JP1.2, R10.2, U$17.3 (PE1)
D2: JP1.3, R11.2
D3: JP1.4, R12.2
D4: JP1.5, R13.2
D5: JP1.6, R14.2
D6: JP1.7, R15.2
D7: JP1.8, R16.2
GND: C1.1, C2.1, C3.-, D1.1 (A), D2.1 (A), D3.1 (A), D4.1 (A), D5.1 (A), D6.1 (A), D7.1 (A), D8.1 (A), D9.1 (A), D10.1 (A), D11.1 (A), D12.1 (A), D13.1 (A), D14.1 (A), D15.1 (A), D16.1 (A), D17.1 (A), D18.1 (A), D19.1 (A), D20.1 (A), D21.1 (A), D22.1 (A), D23.A, IC3.GND, J1.GND, J1.GNDBREAK, JP2.7, JP4.4, JP4.5, JP7.1, JP7.2, JP7.3, JP7.4, JP8.6, POWER.P$2, R23.1, R25.1, R29.1, R34.1, R36.1, R41.1, S1.1, S1.2, U2.7 (GND7), U2.18 (GND18), U2.21 (GND21), U$1.GND, U$2.P$5 (GND), U$3.P$2 (GND), U$4.7 (GND), U$9.1, U$11.4 (V-), U$12.4 (V-), U$13.P$3 (PGND), U$13.P$9 (GND), U$16.4 (V-), U$17.22 (GND1), U$17.53 (GND2), U$17.63 (GND3), U$21.13 (GND)
HIGH_5V_REG: IC3.OUT, U$6.P$1 (S1)
LCD0: U$4.3 (QA), U$9.7
LCD1: U$4.4 (QB), U$9.8
LCD2: U$4.5 (QC), U$9.9
LCD3: U$4.6 (QD), U$9.10
LCD4: U$4.10 (QE), U$9.11
LCD5: U$4.11 (QF), U$9.12
LCD6: U$4.12 (QG), U$9.13
LCD7: U$4.13 (QH), U$9.14
MISO: R37.1
MOSI: R40.2
unnamed: U2.16 (USBDM), U$1.D-
unnamed: U2.15 (USBDP), U$1.D+
unnamed: C2.2, Y1.P$2 (2)
unnamed: C1.2, Y1.P$1 (1)
unnamed: D1.3 (C), R1.1
unnamed: D2.3 (C), R2.1
unnamed: D3.3 (C), R3.1
unnamed: D4.3 (C), R4.1
unnamed: D5.3 (C), R5.1
unnamed: D6.3 (C), R6.1
unnamed: D7.3 (C), R7.1
unnamed: D8.3 (C), R8.1
unnamed: D9.3 (C), R9.1
unnamed: D10.3 (C), R10.1
unnamed: D11.3 (C), R11.1
unnamed: D12.3 (C), R12.1
unnamed: D13.3 (C), R13.1
unnamed: D14.3 (C), R14.1
unnamed: D15.3 (C), R15.1
unnamed: D22.3 (C), R16.1
unnamed: D16.3 (C), R17.1
unnamed: D17.3 (C), R18.1
unnamed: D18.3 (C), R19.1
unnamed: D19.3 (C), R20.1
unnamed: D20.3 (C), R21.1
unnamed: D21.3 (C), R22.1
unnamed: U$1.VBUS, U$10.1
unnamed: U$4.1 (A1), U$4.2 (A2)
unnamed: R31.1, U$7.1 (G), U$12.7 (OUT)
unnamed: F1.2, U$14.3 (D)
unnamed: R25.2, R26.1, U$12.5 (+IN)
unnamed: R28.1, R29.2, U$11.3 (+IN)
unnamed: D24.A, R34.2, U$14.1 (G)
unnamed: JP8.4, R40.1
unnamed: R23.2, R24.1, U$12.3 (+IN)
unnamed: R35.1, R36.2, U$16.3 (+IN)
unnamed: D24.C, R44.1, U$14.2 (S), U$18.2 (S)
unnamed: D25.C, R41.2
unnamed: U$6.P$3 (D2), U$6.P$6 (D1)
unnamed: POWER.P$1, R43.2
unnamed: U$5.P$3 (D2), U$5.P$6 (D1)
unnamed: R30.1, U$8.1 (G), U$12.1 (OUT)
unnamed: JP8.5, R39.2
unnamed: JP8.3, R38.2
unnamed: JP8.1, R37.2
unnamed: R43.1, R44.2, U$18.1 (G)
RESET: JP4.1, R39.1, S1.3, S1.4, U$17.20 (RESET/PG5)
SCK: R38.1
SCL0: JP2.9, R7.2
SDA0: JP2.10, R8.2
USBGATE: R42.1, U$15.1 (G), U$16.1 (OUT)
USB_5V: U$10.2, U$15.3 (D)
V+: U$12.8 (V+)
VCC: U2.20 (VCC)
VCCIO: U2.4 (VCCIO)
VIN: F1.1, J1.PWR, JP4.6
VIN_F: IC3.IN, R28.2, R32.2, R35.2, R42.2, U$5.P$1 (S1), U$15.2 (S), U$18.3 (D)

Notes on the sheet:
Reverse Polarity Protection
USBGATE low when no Vin applied
5V regulator
3.3V regulator

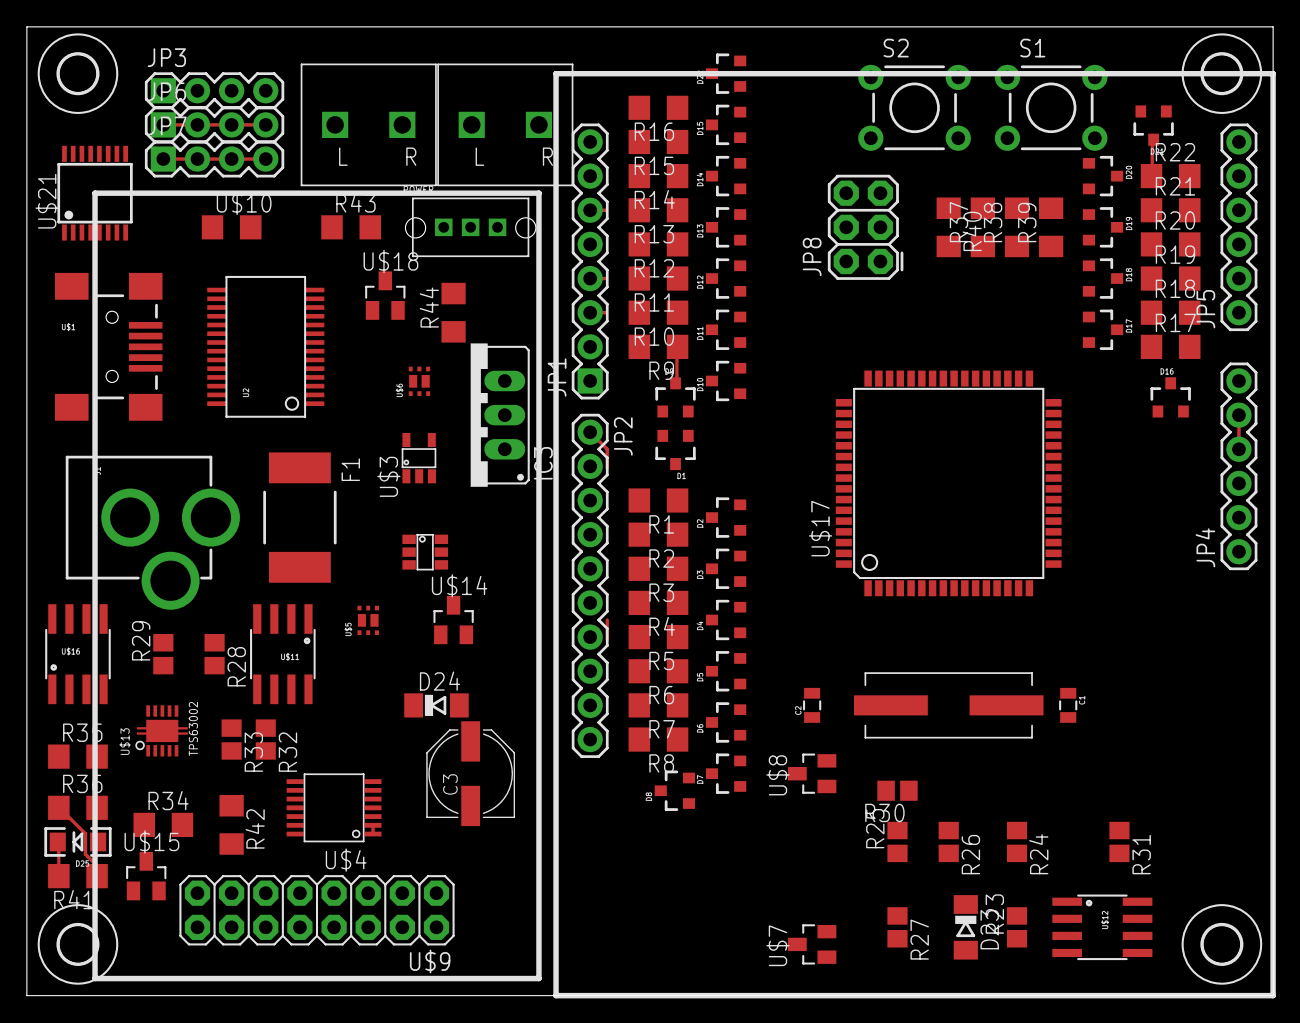
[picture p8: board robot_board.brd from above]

Board: 2 copper layers, 92.7 x 72.1 mm, 113 parts (0 on the bottom side), 91 nets.

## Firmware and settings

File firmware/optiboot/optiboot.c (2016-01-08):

/**********************************************************/
/* Optiboot bootloader for Arduino                        */
/*                                                        */
/* http://optiboot.googlecode.com                         */
/*                                                        */
/* Arduino-maintained version : See README.TXT            */
/* http://code.google.com/p/arduino/                      */
/*  It is the intent that changes not relevant to the     */
/*  Arduino production envionment get moved from the      */
/*  optiboot project to the arduino project in "lumps."   */
/*                                                        */
/* Heavily optimized bootloader that is faster and        */
/* smaller than the Arduino standard bootloader           */
/*                                                        */
/* Enhancements:                                          */
/*   Fits in 512 bytes, saving 1.5K of code space         */
/*   Background page erasing speeds up programming        */
/*   Higher baud rate speeds up programming               */
/*   Written almost entirely in C                         */
/*   Customisable timeout with accurate timeconstant      */
/*   Optional virtual UART. No hardware UART required.    */
/*   Optional virtual boot partition for devices without. */
/*                                                        */
/* What you lose:                                         */
/*   Implements a skeleton STK500 protocol which is       */
/*     missing several features including EEPROM          */
/*     programming and non-page-aligned writes            */
/*   High baud rate breaks compatibility with standard    */
/*     Arduino flash settings                             */
/*                                                        */
/* Fully supported:                                       */
/*   ATmega168 based devices  (Diecimila etc)             */
/*   ATmega328P based devices (Duemilanove etc)           */
/*                                                        */
/* Beta test (believed working.)                          */
/*   ATmega8 based devices (Arduino legacy)               */
/*   ATmega328 non-picopower devices                      */
/*   ATmega644P based devices (Sanguino)                  */
/*   ATmega1284P based devices                            */
/*   ATmega1280 based devices (Arduino Mega)              */
/*                                                        */
/* Alpha test                                             */
/*   ATmega32                                             */
/*                                                        */
/* Work in progress:                                      */
/*   ATtiny84 based devices (Luminet)                     */
/*                                                        */
/* Does not support:                                      */
/*   USB based devices (eg. Teensy, Leonardo)             */
/*                                                        */
/* Assumptions:                                           */
/*   The code makes several assumptions that reduce the   */
/*   code size. They are all true after a hardware reset, */
/*   but may not be true if the bootloader is called by   */
/*   other means or on other hardware.                    */
/*     No interrupts can occur                            */
/*     UART and Timer 1 are set to their reset state      */
/*     SP points to RAMEND                                */
/*                                                        */
/*                                                        */
/* This program is free software; you can redistribute it */
/* and/or modify it under the terms of the GNU General    */
/* Public License as published by the Free Software       */
/* Foundation; either version 2 of the License, or        */
/* (at your option) any later version.                    */
/*                                                        */
/* This program is distributed in the hope that it will   */
/* be useful, but WITHOUT ANY WARRANTY; without even the  */
/* implied warranty of MERCHANTABILITY or FITNESS FOR A   */
/* PARTICULAR PURPOSE.  See the GNU General Public        */
/* License for more details.                              */
/*                                                        */
/* You should have received a copy of the GNU General     */
/* Public License along with this program; if not, write  */
/* to the Free Software Foundation, Inc.,                 */
/* 59 Temple Place, Suite 330, Boston, MA  02111-1307 USA */
/*                                                        */
/* Licence can be viewed at                               */
/* http://www.fsf.org/licenses/gpl.txt                    */
/*                                                        */
/**********************************************************/


/**********************************************************/
/*                                                        */
/* Optional defines:                                      */
/*                                                        */
/**********************************************************/
/*                                                        */
/* BIG_BOOT:                                              */
/* Build a 1k bootloader, not 512 bytes. This turns on    */
/* extra functionality.                                   */
/*                                                        */
/* BAUD_RATE:                                             */
/* Set bootloader baud rate.                              */
/*                                                        */
/* LUDICROUS_SPEED:                                       */
/* 230400 baud :-)                                        */
/*                                                        */
/* SOFT_UART:                                             */
/* Use AVR305 soft-UART instead of hardware UART.         */
/*                                                        */
/* LED_START_FLASHES:                                     */
/* Number of LED flashes on bootup.                       */
/*                                                        */
/* LED_DATA_FLASH:                                        */
/* Flash LED when transferring data. For boards without   */
/* TX or RX LEDs, or for people who like blinky lights.   */
/*                                                        */
/* SUPPORT_EEPROM:                                        */
/* Support reading and writing from EEPROM. This is not   */
/* used by Arduino, so off by default.                    */
/*                                                        */
/* TIMEOUT_MS:                                            */
/* Bootloader timeout period, in milliseconds.            */
/* 500,1000,2000,4000,8000 supported.                     */
/*                                                        */
/* UART:                                                  */
/* UART number (0..n) for devices with more than          */
/* one hardware uart (644P, 1284P, etc)                   */
/*                                                        */
/**********************************************************/



#define OPTIBOOT_MAJVER 5
#define OPTIBOOT_MINVER 0

#define MAKESTR(a) #a
#define MAKEVER(a, b) MAKESTR(a*256+b)

asm("  .section .version\n"
    "optiboot_version:  .word " MAKEVER(OPTIBOOT_MAJVER, OPTIBOOT_MINVER) "\n"
    "  .section .text\n");


#include <inttypes.h>
#include <avr/io.h>
#include <avr/pgmspace.h>
#include <util/delay.h>

// <avr/boot.h> uses sts instructions, but this version uses out instructions
// This saves cycles and program memory.
#include "boot.h"

// We don't use <avr/wdt.h> as those routines have interrupt overhead we don't need.

#include "pin_defs.h"
#include "stk500.h"
#include "globals.h"

#ifndef LED_START_FLASHES
#define LED_START_FLASHES 0
#endif

#ifdef LUDICROUS_SPEED
#define BAUD_RATE 230400L
#endif

/* set the UART baud rate defaults */
#ifndef BAUD_RATE
#if F_CPU >= 8000000L
#define BAUD_RATE   115200L // Highest rate Avrdude win32 will support
#elsif F_CPU >= 1000000L
#define BAUD_RATE   9600L   // 19200 also supported, but with significant error
#elsif F_CPU >= 128000L
#define BAUD_RATE   4800L   // Good for 128kHz internal RC
#else
#define BAUD_RATE 1200L     // Good even at 32768Hz
#endif
#endif

#ifndef UART
#define UART 0
#endif

#define BAUD_SETTING (( (F_CPU + BAUD_RATE * 4L) / ((BAUD_RATE * 8L))) - 1 )
#define BAUD_ACTUAL (F_CPU/(8 * ((BAUD_SETTING)+1)))
#define BAUD_ERROR (( 100*(BAUD_RATE - BAUD_ACTUAL) ) / BAUD_RATE)

#if BAUD_ERROR >= 5
#error BAUD_RATE error greater than 5%
#elif BAUD_ERROR <= -5
#error BAUD_RATE error greater than -5%
#elif BAUD_ERROR >= 2
#warning BAUD_RATE error greater than 2%
#elif BAUD_ERROR <= -2
#warning BAUD_RATE error greater than -2%
#endif

#if 0
/* Switch in soft UART for hard baud rates */
/*
 * I don't understand what this was supposed to accomplish, where the
 * constant "280" came from, or why automatically (and perhaps unexpectedly)
 * switching to a soft uart is a good thing, so I'm undoing this in favor
 * of a range check using the same calc used to config the BRG...
 */
#if (F_CPU/BAUD_RATE) > 280 // > 57600 for 16MHz
#ifndef SOFT_UART
#define SOFT_UART
#endif
#endif
#else // 0
#if (F_CPU + BAUD_RATE * 4L) / (BAUD_RATE * 8L) - 1 > 250
#error Unachievable baud rate (too slow) BAUD_RATE 
#endif // baud rate slow check
#if (F_CPU + BAUD_RATE * 4L) / (BAUD_RATE * 8L) - 1 < 3
#error Unachievable baud rate (too fast) BAUD_RATE 
#endif // baud rate fastn check
#endif

/* Watchdog settings */
#define WATCHDOG_OFF    (0)
#define WATCHDOG_16MS   (_BV(WDE))
#define WATCHDOG_32MS   (_BV(WDP0) | _BV(WDE))
#define WATCHDOG_64MS   (_BV(WDP1) | _BV(WDE))
#define WATCHDOG_125MS  (_BV(WDP1) | _BV(WDP0) | _BV(WDE))
#define WATCHDOG_250MS  (_BV(WDP2) | _BV(WDE))
#define WATCHDOG_500MS  (_BV(WDP2) | _BV(WDP0) | _BV(WDE))
#define WATCHDOG_1S     (_BV(WDP2) | _BV(WDP1) | _BV(WDE))
#define WATCHDOG_2S     (_BV(WDP2) | _BV(WDP1) | _BV(WDP0) | _BV(WDE))
#ifndef __AVR_ATmega8__
#define WATCHDOG_4S     (_BV(WDP3) | _BV(WDE))
#define WATCHDOG_8S     (_BV(WDP3) | _BV(WDP0) | _BV(WDE))
#endif

/* Function Prototypes */
/* The main function is in init9, which removes the interrupt vector table */
/* we don't need. It is also 'naked', which means the compiler does not    */
/* generate any entry or exit code itself. */
//int main(void) __attribute__ ((OS_main)) __attribute__ ((section (".init9")));
int main(void);
void putch(char);
uint8_t getch(void);
static inline void getNch(uint8_t); /* "static inline" is a compiler hint to reduce code size */
void verifySpace();
static inline void flash_led(uint8_t);
uint8_t getLen();
static inline void watchdogReset();
void watchdogConfig(uint8_t x);
#ifdef SOFT_UART
void uartDelay() __attribute__ ((naked));
#endif
void appStart(uint8_t rstFlags) __attribute__ ((naked));
void debug_mode();

/*
 * NRWW memory
 * Addresses below NRWW (Non-Read-While-Write) can be programmed while
 * continuing to run code from flash, slightly speeding up programming
 * time.  Beware that Atmel data sheets specify this as a WORD address,
 * while optiboot will be comparing against a 16-bit byte address.  This
 * means that on a part with 128kB of memory, the upper part of the lower
 * 64k will get NRWW processing as well, even though it doesn't need it.
 * That's OK.  In fact, you can disable the overlapping processing for
 * a part entirely by setting NRWWSTART to zero.  This reduces code
 * space a bit, at the expense of being slightly slower, overall.
 *
 * RAMSTART should be self-explanatory.  It's bigger on parts with a
 * lot of peripheral registers.
 */
#if defined(__AVR_ATmega328P__) || defined(__AVR_ATmega32__) || defined(__AVR_ATmega645A__)
#define NRWWSTART (0xE000)
#endif

/* C zero initializes all global variables. However, that requires */
/* These definitions are NOT zero initialized, but that doesn't matter */
/* This allows us to drop the zero init code, saving us memory */
#define buff    ((uint8_t*)(RAMSTART))

/* main program starts here */
int main(void) {
  uint8_t ch;
  uint8_t temp; 

  /*
   * Making these local and in registers prevents the need for initializing
   * them, and also saves space because code no longer stores to memory.
   * (initializing address keeps the compiler happy, but isn't really
   *  necessary, and uses 4 bytes of flash.)
   */
  uint16_t address = 0;
  uint8_t  length;

  // After the zero init loop, this is the first code to run.
  //
  // This code makes the following assumptions:
  //  No interrupts will execute
  //  SP points to RAMEND
  //  r1 contains zero
  //
  // If not, uncomment the following instructions:
  // cli();
  //asm volatile ("clr __zero_reg__");
#if defined(__AVR_ATmega8__) || defined (__AVR_ATmega32__) //|| defined (__AVR_ATmega325PA__)
  SP=RAMEND;  // This is done by hardware reset
#endif

  // Adaboot no-wait mod
  ch = MCUSR;
  MCUSR = 0;
  if (!(ch & _BV(EXTRF))) appStart(ch);

#if LED_START_FLASHES > 0
  // Set up Timer 1 for timeout counter
  TCCR1B = _BV(CS12) | _BV(CS10); // div 1024
#endif

  // Set up watchdog to trigger after 500ms
  watchdogConfig(WATCHDOG_1S);

#if (LED_START_FLASHES > 0) || defined(LED_DATA_FLASH)
  /* Set LED pin as output */
  //LED_DDR |= _BV(LED);
#endif

#ifdef SOFT_UART
  /* Set TX pin as output */
  UART_DDR |= _BV(UART_TX_BIT);
#endif

#if LED_START_FLASHES > 0
  /* Flash onboard LED to signal entering of bootloader */
  flash_led(LED_START_FLASHES * 2);
#endif

  init();
  if(get_btn()) {
     /* Get MCUCR*/ 
     temp = MCUCR; 
     /* Enable change of Interrupt Vectors */ 
     MCUCR = temp|(1<<IVCE); 
     /* Move interrupts to Boot Flash section */ 
     MCUCR = temp|(1<<IVSEL);

     watchdogConfig(WATCHDOG_OFF);
     init_servo();
     debug_mode();
  }

  led_on(0);
  clear_screen();
  //print_string("testing",7);
  /*clear_screen();
  while(1){
     print_string("testing", 7);
     _delay_ms(500);
     clear_screen();
     _delay_ms(500);
  }*/

  /* Forever loop */
  for (;;) {
    /* get character from UART */
    ch = getch();

    if(ch == STK_GET_PARAMETER) {
      unsigned char which = getch();
      verifySpace();
      if (which == 0x82) {
	/*
	 * Send optiboot version as "minor SW version"
	 */
	putch(OPTIBOOT_MINVER);
      } else if (which == 0x81) {
	  putch(OPTIBOOT_MAJVER);
      } else {
	/*
	 * GET PARAMETER returns a generic 0x03 reply for
         * other parameters - enough to keep Avrdude happy
	 */
	putch(0x03);
      }
    }
    else if(ch == STK_SET_DEVICE) {
      // SET DEVICE is ignored
      getNch(20);
    }
    else if(ch == STK_SET_DEVICE_EXT) {
      // SET DEVICE EXT is ignored
      getNch(5);
    }
    else if(ch == STK_LOAD_ADDRESS) {
      watchdogReset();
      // LOAD ADDRESS
      uint16_t newAddress;
      newAddress = getch();
      newAddress = (newAddress & 0xff) | (getch() << 8);
#ifdef RAMPZ
      // Transfer top bit to RAMPZ
      RAMPZ = (newAddress & 0x8000) ? 1 : 0;
#endif
      newAddress += newAddress; // Convert from word address to byte address
      address = newAddress;
      verifySpace();
    }
    else if(ch == STK_UNIVERSAL) {
      // UNIVERSAL command is ignored
      getNch(4);
      putch(0x00);
    }
    /* Write memory, length is big endian and is in bytes */
    else if(ch == STK_PROG_PAGE) {
      // PROGRAM PAGE - we support flash programming only, not EEPROM
      uint8_t *bufPtr;
      uint16_t addrPtr;

      getch();			/* getlen() */
      length = getch();
      getch();

      // If we are in RWW section, immediately start page erase
      if (address < NRWWSTART) __boot_page_erase_short((uint16_t)(void*)address);

      // While that is going on, read in page contents
      bufPtr = buff;
      do *bufPtr++ = getch();
      while (--length);

      // If we are in NRWW section, page erase has to be delayed until now.
      // Todo: Take RAMPZ into account (not doing so just means that we will
      //  treat the top of both "pages" of flash as NRWW, for a slight speed
      //  decrease, so fixing this is not urgent.)
      if (address >= NRWWSTART) __boot_page_erase_short((uint16_t)(void*)address);

      // Read command terminator, start reply
      verifySpace();

      // If only a partial page is to be programmed, the erase might not be complete.
      // So check that here
      boot_spm_busy_wait();

      // Copy buffer into programming buffer
      bufPtr = buff;
      addrPtr = (uint16_t)(void*)address;
      ch = SPM_PAGESIZE / 2;
      do {
        uint16_t a;
        a = *bufPtr++;
        a |= (*bufPtr++) << 8;
        __boot_page_fill_short((uint16_t)(void*)addrPtr,a);
        addrPtr += 2;
      } while (--ch);

      // Write from programming buffer
      __boot_page_write_short((uint16_t)(void*)address);
      boot_spm_busy_wait();

#if defined(RWWSRE)
      // Reenable read access to flash
      boot_rww_enable();
#endif

    }
    /* Read memory block mode, length is big endian.  */
    else if(ch == STK_READ_PAGE) {
      watchdogReset();
      // READ PAGE - we only read flash
      getch();			/* getlen() */
      length = getch();
      getch();

      verifySpace();
      do {
#ifdef VIRTUAL_BOOT_PARTITION
        // Undo vector patch in bottom page so verify passes
        if (address == 0)       ch=rstVect & 0xff;
        else if (address == 1)  ch=rstVect >> 8;
        else if (address == 8)  ch=wdtVect & 0xff;
        else if (address == 9) ch=wdtVect >> 8;
        else ch = pgm_read_byte_near(address);
        address++;
#elif defined(RAMPZ)
        // Since RAMPZ should already be set, we need to use EPLM directly.
        // Also, we can use the autoincrement version of lpm to update "address"
        //      do putch(pgm_read_byte_near(address++));
        //      while (--length);
        // read a Flash and increment the address (may increment RAMPZ)
        __asm__ ("elpm %0,Z+\n" : "=r" (ch), "=z" (address): "1" (address));
#else
        // read a Flash byte and increment the address
        __asm__ ("lpm %0,Z+\n" : "=r" (ch), "=z" (address): "1" (address));
#endif
        putch(ch);
      } while (--length);
    }

    /* Get device signature bytes  */
    else if(ch == STK_READ_SIGN) {
      // READ SIGN - return what Avrdude wants to hear
      verifySpace();
      putch(SIGNATURE_0);
      putch(SIGNATURE_1);
      putch(SIGNATURE_2);
    }
    else if (ch == STK_LEAVE_PROGMODE) { /* 'Q' */
      // Adaboot no-wait mod
      verifySpace();
      putch(STK_OK);
      watchdogConfig(WATCHDOG_16MS);
    }
    else {
      // This covers the response to commands like STK_ENTER_PROGMODE
      verifySpace();
    }
    putch(STK_OK);
  }
}

void putch(char ch) {
  __asm__ __volatile__ (
    "   com %[ch]\n" // ones complement, carry set
    "   sec\n"
    "1: brcc 2f\n"
    "   cbi %[uartPort],%[uartBit]\n"
    "   rjmp 3f\n"
    "2: sbi %[uartPort],%[uartBit]\n"
    "   nop\n"
    "3: rcall uartDelay\n"
    "   rcall uartDelay\n"
    "   lsr %[ch]\n"
    "   dec %[bitcnt]\n"
    "   brne 1b\n"
    :
    :
      [bitcnt] "d" (10),
      [ch] "r" (ch),
      [uartPort] "I" (_SFR_IO_ADDR(UART_PORT)),
      [uartBit] "I" (UART_TX_BIT)
    :
      "r25"
  );
}

uint8_t getch(void) {
  uint8_t ch;

  /*
#ifdef LED_DATA_FLASH
#if defined(__AVR_ATmega8__) || defined (__AVR_ATmega32__)
  LED_PORT ^= _BV(LED);
#else
  LED_PIN |= _BV(LED);
#endif
#endif
*/

  __asm__ __volatile__ (
    "1: sbic  %[uartPin],%[uartBit]\n"  // Wait for start edge
    "   rjmp  1b\n"
    "   rcall uartDelay\n"          // Get to middle of start bit
    "2: rcall uartDelay\n"              // Wait 1 bit period
    "   rcall uartDelay\n"              // Wait 1 bit period
    "   clc\n"
    "   sbic  %[uartPin],%[uartBit]\n"
    "   sec\n"
    "   dec   %[bitCnt]\n"
    "   breq  3f\n"
    "   ror   %[ch]\n"
    "   rjmp  2b\n"
    "3:\n"
    :
      [ch] "=r" (ch)
    :
      [bitCnt] "d" (9),
      [uartPin] "I" (_SFR_IO_ADDR(UART_PIN)),
      [uartBit] "I" (UART_RX_BIT)
    :
      "r25"
);

  /*
#ifdef LED_DATA_FLASH
#if defined(__AVR_ATmega8__) || defined (__AVR_ATmega32__)
  LED_PORT ^= _BV(LED);
#else
  LED_PIN |= _BV(LED);
#endif
#endif
*/

  return ch;
}

#ifdef SOFT_UART
// AVR305 equation: #define UART_B_VALUE (((F_CPU/BAUD_RATE)-23)/6)
// Adding 3 to numerator simulates nearest rounding for more accurate baud rates
#define UART_B_VALUE (((F_CPU/BAUD_RATE)-20)/6)
#if UART_B_VALUE > 255
#error Baud rate too slow for soft UART
#endif

void uartDelay() {
  __asm__ __volatile__ (
    "ldi r25,%[count]\n"
    "1:dec r25\n"
    "brne 1b\n"
    "ret\n"
    ::[count] "M" (UART_B_VALUE)
  );
}
#endif

void getNch(uint8_t count) {
  do {
     //led_on(1);
     getch();
     //led_off(1);
  } while (--count);
  verifySpace();
}

void verifySpace() {
  if (getch() != CRC_EOP) {
    watchdogConfig(WATCHDOG_16MS);    // shorten WD timeout
    //watchdogConfig(WATCHDOG_32MS);    // shorten WD timeout
    while (1)			      // and busy-loop so that WD causes
      ;				      //  a reset and app start.
  }
  putch(STK_INSYNC);
}

#if LED_START_FLASHES > 0
void flash_led(uint8_t count) {
  do {
    TCNT1 = -(F_CPU/(1024*16));
    TIFR1 = _BV(TOV1);
    while(!(TIFR1 & _BV(TOV1)));
#if defined(__AVR_ATmega8__)  || defined (__AVR_ATmega32__)
    //LED_PORT ^= _BV(LED);
#else
    //LED_PIN |= _BV(LED);
#endif
    watchdogReset();
  } while (--count);
}
#endif

// Watchdog functions. These are only safe with interrupts turned off.
void watchdogReset() {
  __asm__ __volatile__ (
    "wdr\n"
  );
}

void watchdogConfig(uint8_t x) {
  WDTCR = _BV(WDCE) | _BV(WDE);
  WDTCR = x;
}
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

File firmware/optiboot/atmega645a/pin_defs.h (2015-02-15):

/*------------------------------------------------------------------------ */
#if defined(__AVR_ATmega645A__)
/*------------------------------------------------------------------------ */

/* Onboard LED is connected to pin PB5 in Arduino NG, Diecimila, and Duemilanove
 */ 
#if !defined(LED)
#define LED B5
#endif

/* Ports for soft UART */
#ifdef SOFT_UART
#define UART_PORT   PORTD
#define UART_PIN    PIND
#define UART_DDR    DDRD
#define UART_TX_BIT 2
#define UART_RX_BIT 3
#endif
#endif

/*
 * ------------------------------------------------------------------------
 * A bunch of macros to enable the LED to be specifed as "B5" for bit 5 
 * of port B, and similar.
 */

#define A0 0x100
#define A1 0x101
#define A2 0x102
#define A3 0x103
#define A4 0x104
#define A5 0x105
#define A6 0x106
#define A7 0x107

#define B0 0x200
#define B1 0x201
#define B2 0x202
#define B3 0x203
#define B4 0x204
#define B5 0x205
#define B6 0x206
#define B7 0x207

#define C0 0x300
#define C1 0x301
#define C2 0x302
#define C3 0x303
#define C4 0x304
#define C5 0x305
#define C6 0x306
#define C7 0x307

#define D0 0x400
#define D1 0x401
#define D2 0x402
#define D3 0x403
#define D4 0x404
#define D5 0x405
#define D6 0x406
#define D7 0x407

#define E0 0x500
#define E1 0x501
#define E2 0x502
#define E3 0x503
#define E4 0x504
#define E5 0x505
#define E6 0x506
#define E7 0x507

#define F0 0x600
#define F1 0x601
#define F2 0x602
#define F3 0x603
#define F4 0x604
#define F5 0x605
#define F6 0x606
#define F7 0x607

#define G0 0x700
#define G1 0x701
#define G2 0x702
#define G3 0x703
#define G4 0x704
#define G5 0x705
#define G6 0x706
#define G7 0x707

#define H0 0x800
#define H1 0x801
#define H2 0x802
#define H3 0x803
#define H4 0x804
#define H5 0x805
#define H6 0x806
#define H7 0x807

#define J0 0xA00
#define J1 0xA01
#define J2 0xA02
#define J3 0xA03
#define J4 0xA04
#define J5 0xA05
#define J6 0xA06
#define J7 0xA07

#define K0 0xB00
#define K1 0xB01
#define K2 0xB02
#define K3 0xB03
#define K4 0xB04
#define K5 0xB05
#define K6 0xB06
#define K7 0xB07

#define L0 0xC00
#define L1 0xC01
#define L2 0xC02
#define L3 0xC03
#define L4 0xC04
#define L5 0xC05
#define L6 0xC06
#define L7 0xC07



#if LED == B0
#undef LED
#define LED_DDR     DDRB
#define LED_PORT    PORTB
#define LED_PIN     PINB
#define LED	    PINB0
#elif LED == B1
#undef LED
#define LED_DDR     DDRB
#define LED_PORT    PORTB
#define LED_PIN     PINB
#define LED	    PINB1
#elif LED == B2
#undef LED
#define LED_DDR     DDRB
#define LED_PORT    PORTB
#define LED_PIN     PINB
#define LED	    PINB2
#elif LED == B3
#undef LED
#define LED_DDR     DDRB
#define LED_PORT    PORTB
#define LED_PIN     PINB
#define LED	    PINB3
#elif LED == B4
#undef LED
#define LED_DDR     DDRB
#define LED_PORT    PORTB
#define LED_PIN     PINB
#define LED	    PINB4
#elif LED == B5
#undef LED
#define LED_DDR     DDRB
#define LED_PORT    PORTB
#define LED_PIN     PINB
#define LED	    PINB5
#elif LED == B6
#undef LED
#define LED_DDR     DDRB
#define LED_PORT    PORTB
#define LED_PIN     PINB
#define LED	    PINB6
#elif LED == B7
#undef LED
#define LED_DDR     DDRB
#define LED_PORT    PORTB
#define LED_PIN     PINB
#define LED	    PINB7

#elif LED == C0
#undef LED
#define LED_DDR     DDRC
#define LED_PORT    PORTC
#define LED_PIN     PINC
#define LED	    PINC0
#elif LED == C1
#undef LED
#define LED_DDR     DDRC
#define LED_PORT    PORTC
#define LED_PIN     PINC
#define LED	    PINC1
#elif LED == C2
#undef LED
#define LED_DDR     DDRC
#define LED_PORT    PORTC
#define LED_PIN     PINC
#define LED	    PINC2
#elif LED == C3
#undef LED
#define LED_DDR     DDRC
#define LED_PORT    PORTC
#define LED_PIN     PINC
#define LED	    PINC3
#elif LED == C4
#undef LED
#define LED_DDR     DDRC
#define LED_PORT    PORTC
#define LED_PIN     PINC
#define LED	    PINC4
#elif LED == C5
#undef LED
#define LED_DDR     DDRC
#define LED_PORT    PORTC
#define LED_PIN     PINC
#define LED	    PINC5
#elif LED == C6
#undef LED
#define LED_DDR     DDRC
#define LED_PORT    PORTC
#define LED_PIN     PINC
#define LED	    PINC6
#elif LED == C7
#undef LED
#define LED_DDR     DDRC
#define LED_PORT    PORTC
#define LED_PIN     PINC
#define LED	    PINC7
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

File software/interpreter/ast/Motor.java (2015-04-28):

package ast;
import visitor.*;

public class Motor extends Machinery implements Settable {
   private int _motorNum;

   public Motor(String id, int motorNum) {
      super(id);
      _motorNum = motorNum;
   }

   public int getMachineNumber()
   {
      return _motorNum;
   }

   public String toSetString(CharSequence seq)
   {
      return String.format("set_motor(%s, %s)", getIdentifier(), seq);
   }

   public <T> T visit(ASTVisitor<T> guest)
   {
      return guest.visit(this);
   }

   public boolean equals(Object o)
   {
      if (o == null)
      {
         return false;
      }
      if (o instanceof Motor)
      {
         Motor other = (Motor)o;
         return other._motorNum == this._motorNum;
      }
      return false;
   }
}

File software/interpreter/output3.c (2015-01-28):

#include <stdio.h>

#define thermometer 0

#define leftServo 0

#define rightServo 1

void start(void)
{
printf("%s\n","Hello! Machine is starting up");
}
void repeatAlways(void)
{
printf("%s%d\n","Thermometer reading is: ",analog(thermometer));
set_servo(leftServo, 15);
set_servo(rightServo, 75);
printf("%s%d\n","Temperature in Celsius is: ",(((analog(thermometer) - 32) * 5) /(float) 9));
}
int main(void) {
start();
while (1) {
repeatAlways();
}
return 0;
}

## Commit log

2014-01-28 initial checkin of board
    [robot_board.brd, robot_board.sch]
2014-01-29 added button call
2014-01-30 check in library and restructured directories
    [robot_board.brd, robot_board.sch]
2014-01-30 updated schematic
    [robot_board.brd, robot_board.sch]
2014-01-30 update libraries
    [robot_board.brd, robot_board.sch]
2014-01-30 added accelerometer device
    [robot_board.brd, robot_board.sch]
2014-01-31 changed board size and added gyro interrupt
    [robot_board.brd, robot_board.sch]
2014-02-02 modified overall layout
    [robot_board.brd, robot_board.sch]
2014-02-02 board spec file
2014-02-02 update board spec
2014-02-02 begin power layout
    [robot_board.brd, robot_board.sch]
2014-02-04 more routing and library updates
    [robot_board.brd, robot_board.sch]
2014-02-04 more routing
    [robot_board.brd, robot_board.sch]
2014-02-06 added Bluetooth module
    [robot_board.brd, robot_board.sch]
2014-02-07 reversed digital/analog pins
    [robot_board.brd, robot_board.sch]
2014-02-08 updated bluetooth
    [robot_board.brd, robot_board.sch]
2014-02-10 updated Bluetooth pinout
    [robot_board.brd, robot_board.sch]
2014-02-12 updated routing
    [robot_board.brd, robot_board.sch]
2014-02-12 fix analog pin ordering error
    [robot_board.brd, robot_board.sch]
2014-02-13 fix servo bug
    [robot_board.brd, robot_board.sch]
2014-02-13 initial check in of gerber files
    [robot_board.GBL, robot_board.GBO, robot_board.GBS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]
2014-02-13 add drill file
2014-02-13 made version directory
    [robot_board.brd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]
2014-02-13 added drill files
2014-02-14 changed resistor values
    [robot_board.brd, robot_board.sch]
2014-02-20 updated resistor values
    [robot_board.brd, robot_board.sch]
2014-03-01 remove old servo code
2014-03-01 blinking LED program
2014-03-05 added latest board revision
    [robot_board.brd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]
2014-03-05 added i2c files
2014-03-05 changed i2c file name
2014-03-07 USB and main power are switched with on/off switch
    [robot_board.brd, robot_board.sch]
2014-03-08 initial i2c library
2014-03-09 before adding 5V i2c resistors
    [robot_board.brd]
2014-03-09 added i2c level shifter
    [robot_board.brd, robot_board.sch]
2014-03-14 revision 2
    [robot_board.brd, robot_board.sch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]
2014-03-24 moved code to v0.1 directory
    [robot_board.brd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]
2014-03-27 v.2 working accelerometer
2014-03-31 fix servo code
    [robot_board.brd, robot_board.sch]
2014-04-25 Add IR interrupt code
    Added code to test pin interrupts with the IR sensor.
    Added a makefile which links in code from the Arduino standard
    libraries.
2014-04-25 Fix arduino libraries
    Copied libraries into the project to eliminate dependence on the arduino
    IDE.
    Removed excess code.
    Generalized interrupt function to work for multiple pins.
2014-04-25 Moved files to firmware directory
    Relocated the files for the IR sensor
2014-04-30 Add IR buffer
    Added code for storing and retrieving data from the IR sensor using a
    buffer.
2014-05-21 updated some files because there were errors when compiling. Might need to make some more changes due to this as well. minChgStrings.add(currPerm.substring(0,k) + letter + currPerm.substring(k));
    [Parser.java]
2014-10-06 Left a couple of comments for TO DOs: Need to Scan not =, or !=
2014-10-13 Bug fixes and inclusion of arduino_lib.c library dummy library functions. Bug fixes: Tested parsing and outputing and linking machinery of motors, pins Initialized the environment with a button and l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
    [Parser.java, arduino_lib.c]
2014-10-28 Redacting previous changes:
    1) the = symbol is no longer contextual. Meaning that = always means assignment
    and equals is always equality.
    2) For equality, the grammar includes eq and equals as the same thing, and
    noteq and notequals as the same thing
    [Parser.java]
2014-10-30 When conditionas now accept get button
2015-01-07 checkin of 3rd revision
    [robot_board.brd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]
2015-01-12 added i2c file to bootloader
2015-01-26 updated servo library
2015-01-26 updated Makefile and function prototypes
2015-01-26 renamed old i2c testing files
2015-01-26 updated motor and servo code
2015-01-28 updated motor call
2015-01-28 Fixed null pointer exception with assignments. Mixed up TK_EQ with TK_ASSIGN in the parser
    [Parser.java]
2015-01-28 Patched tricky identifier issues. Identifier issues include a plain ID, an array access, and a function call
    [Parser.java]
2015-01-29 Semi-colons and new lines fixed for assignment statements Scanner eats +=, -=, *=, and /=
    [arduino_lib.c]
2015-01-29 Initial Working script for compilation on board
2015-01-29 added led() function
2015-01-30 Button and 2 LEDs work
2015-01-30 updated servo functions
2015-02-02 board revision 4
    [current_bom.csv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]
2015-02-04 auto detect board in Makefile on Mac OS
2015-02-06 working board autodetect on Mac
2015-02-06 updated accelerometer functions
2015-02-06 call interpreter from IDE. Allows buzz code testing.
    [Bumblebee.java]
2015-02-07 added help button and basic syntax help information
2015-02-13 updated i2c library to accept device id
2015-02-19 The Main contains a driver to run the Interpreter
2015-02-19 Standardize error messages to have [Line %d]
    [Parser.java]
2015-02-19 Digital pins now associated with 1 pin
2015-02-22 working Upload button
2015-02-23 make TX pin an output
2015-02-24 Lower case and upper case leds ex. LED0 and led1
2015-02-25 Included line numbers for lonely identifier error msgs
    [Parser.java]
2015-02-27 highlight line with error
    [Bumblebee.java]
2015-03-05 Added border with red color when board not detected. And border with green color and new text when board detected.
2015-04-21 Duplicate declarations of machinery is prohibited In addition, IR is included and Gyroscope -> Accelerometer
2015-04-28 Accelerometer code updated. Waiting on IR
2015-08-06 added digital output function prototypes
2015-08-06 updated switch functions
2015-09-22 enable accelerometer
2016-01-08 initial checkin of board file for Arduino IDE

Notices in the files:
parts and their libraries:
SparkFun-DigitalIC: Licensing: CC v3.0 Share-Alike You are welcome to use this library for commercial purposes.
